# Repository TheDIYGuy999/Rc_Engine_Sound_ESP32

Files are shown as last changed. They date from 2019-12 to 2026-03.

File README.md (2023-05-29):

# This is an Arduino RC engine sound & light controller for ESP32





It's based on the ATmega 328 version: https://github.com/TheDIYGuy999/Rc_Engine_Sound
and on bitlunis Halloween example: https://github.com/bitluni/MotionPumpkin

Wiring and software installation instructions see further down.
Arduino IDE or Visual Studio Code (with Platform IO extension) are supported.

Video series: https://www.youtube.com/playlist?list=PLGO5EJJClJBCjIvu8frS7LrEU3H2Yz_so

************************************************************************
You can find the changes in the [Changelog](documentation/Changelog.md).
************************************************************************

Discussion and support thread (in German & English): https://www.rc-modellbau-portal.de/index.php?threads/esp32-arduino-rc-sound-und-licht-controller.7183/

Fully assembled, tested and working 30 pin SMD version with switch mode PSU & display connector.
Order it here: https://www.pcbway.com/project/shareproject/Arduino_RC_engine_sound_light_controller_for_ESP32_a9334731.html


New: STL data for nice 3D printed housing available:
https://thediyguy999.github.io/TheDIYGuy999_ESP32_Web_Flasher/products.html
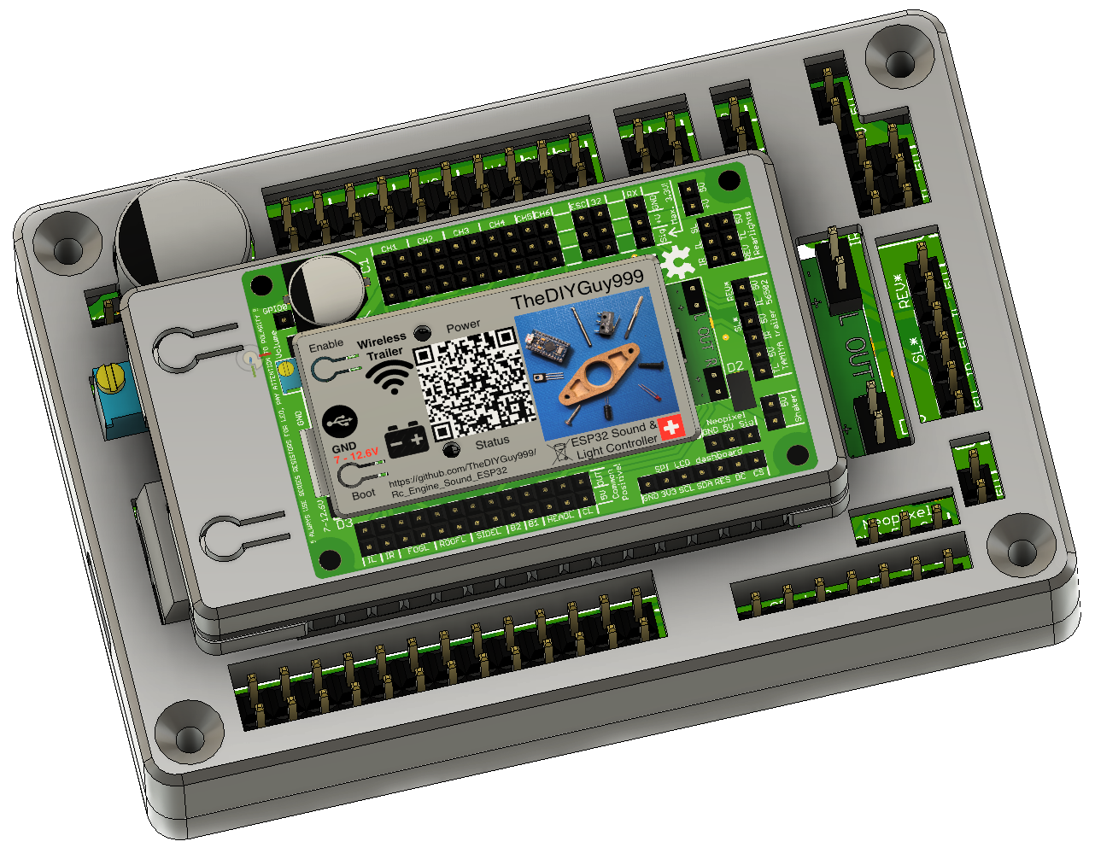
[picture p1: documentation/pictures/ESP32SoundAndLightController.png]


New: Compact version for trailer or tractor:
https://thediyguy999.github.io/TheDIYGuy999_ESP32_Web_Flasher/products.html
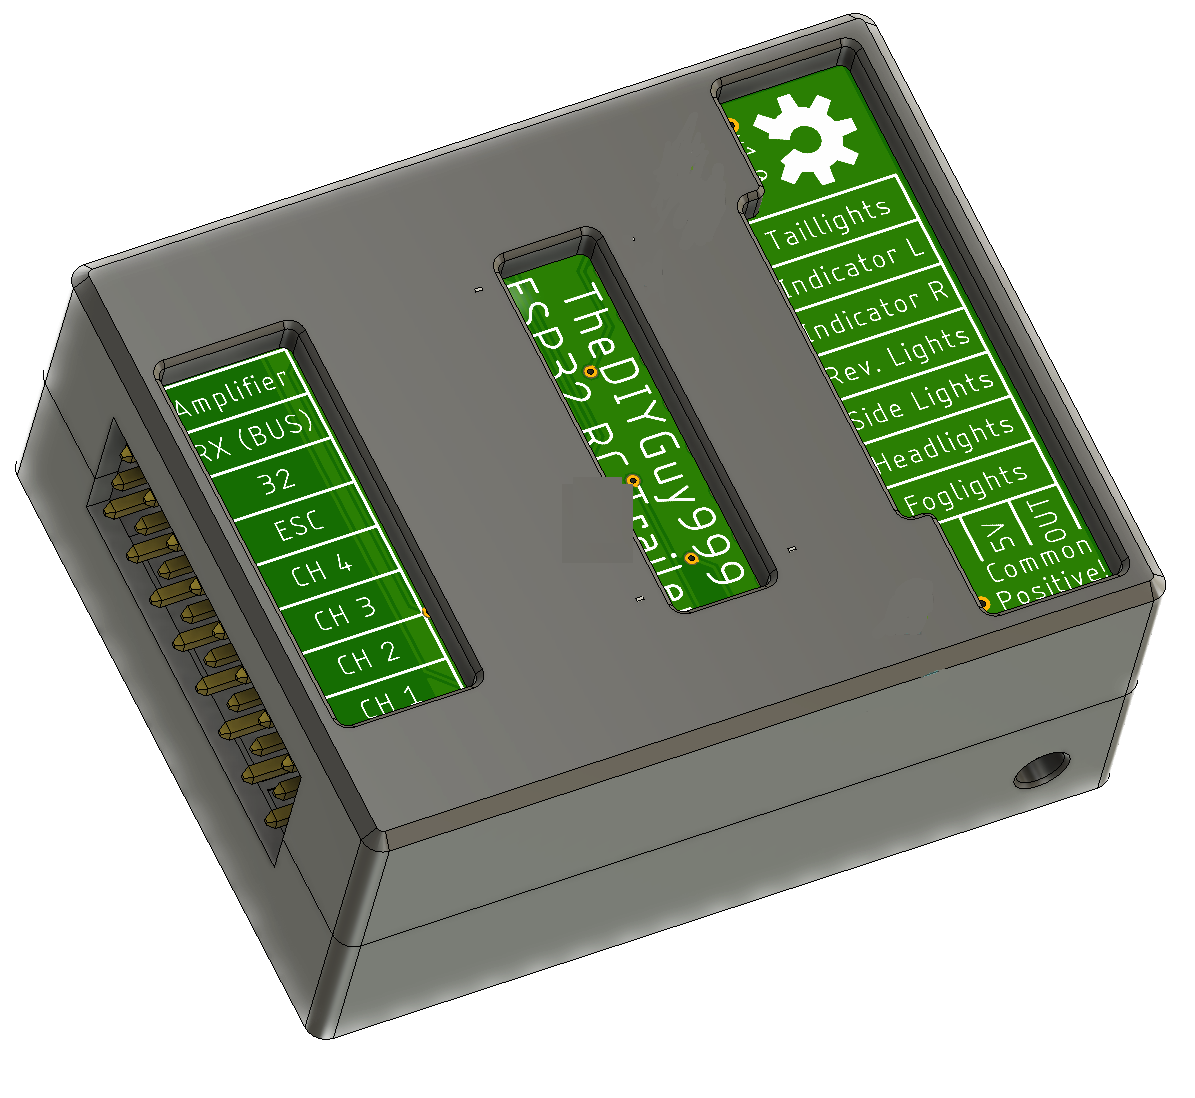
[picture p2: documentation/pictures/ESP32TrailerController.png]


New: RZ7886 7A ESC:
https://thediyguy999.github.io/TheDIYGuy999_ESP32_Web_Flasher/products.html
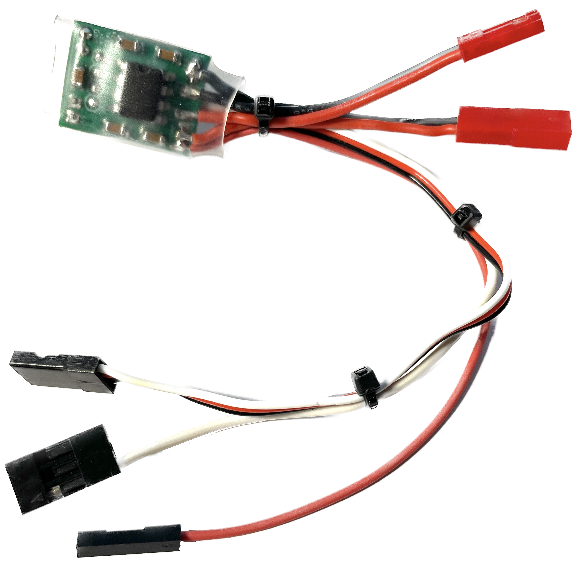
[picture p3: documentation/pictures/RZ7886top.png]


New: wireless built-in configuration website 192.168.4.1
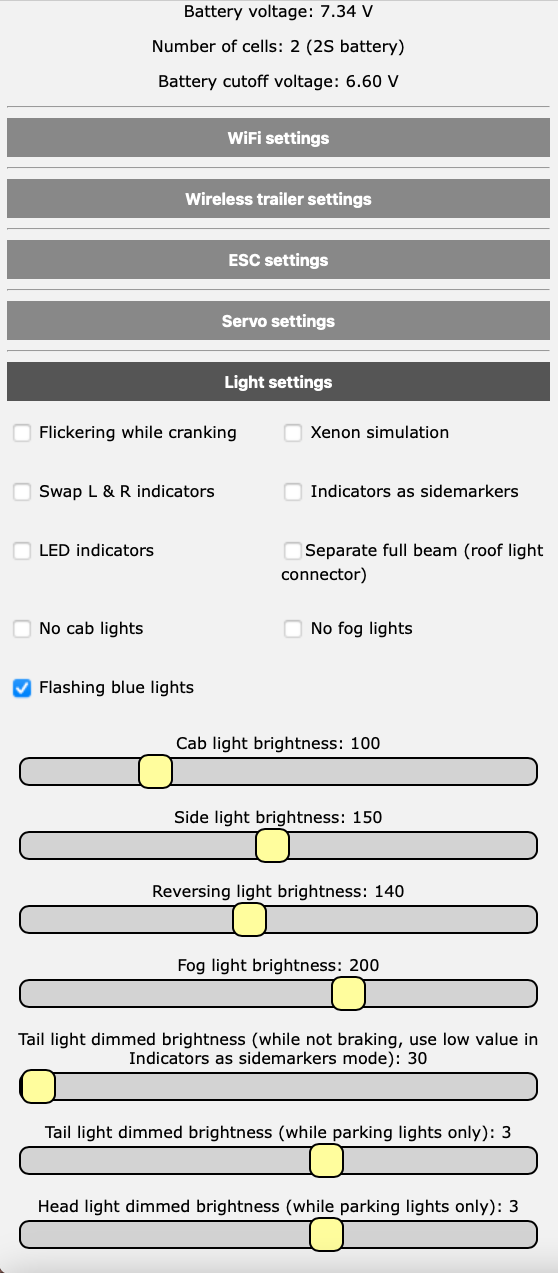
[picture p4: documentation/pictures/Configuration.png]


New: LCD dashboard (original by Frevic)
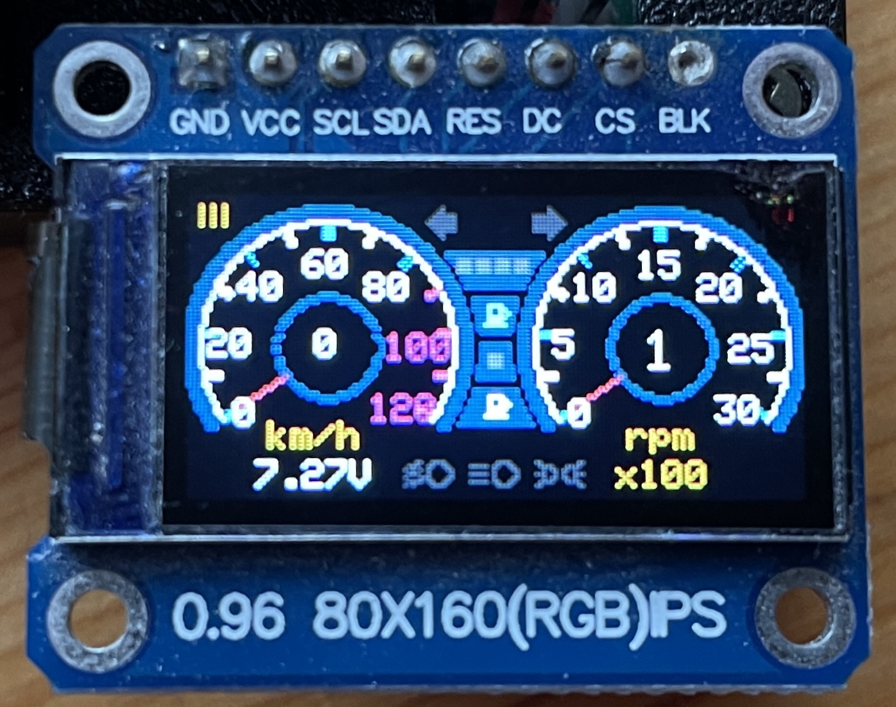
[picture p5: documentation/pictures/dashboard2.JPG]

https://www.facebook.com/profile.php?id=100066616574355

LCD dashboard (original by Gamadril)
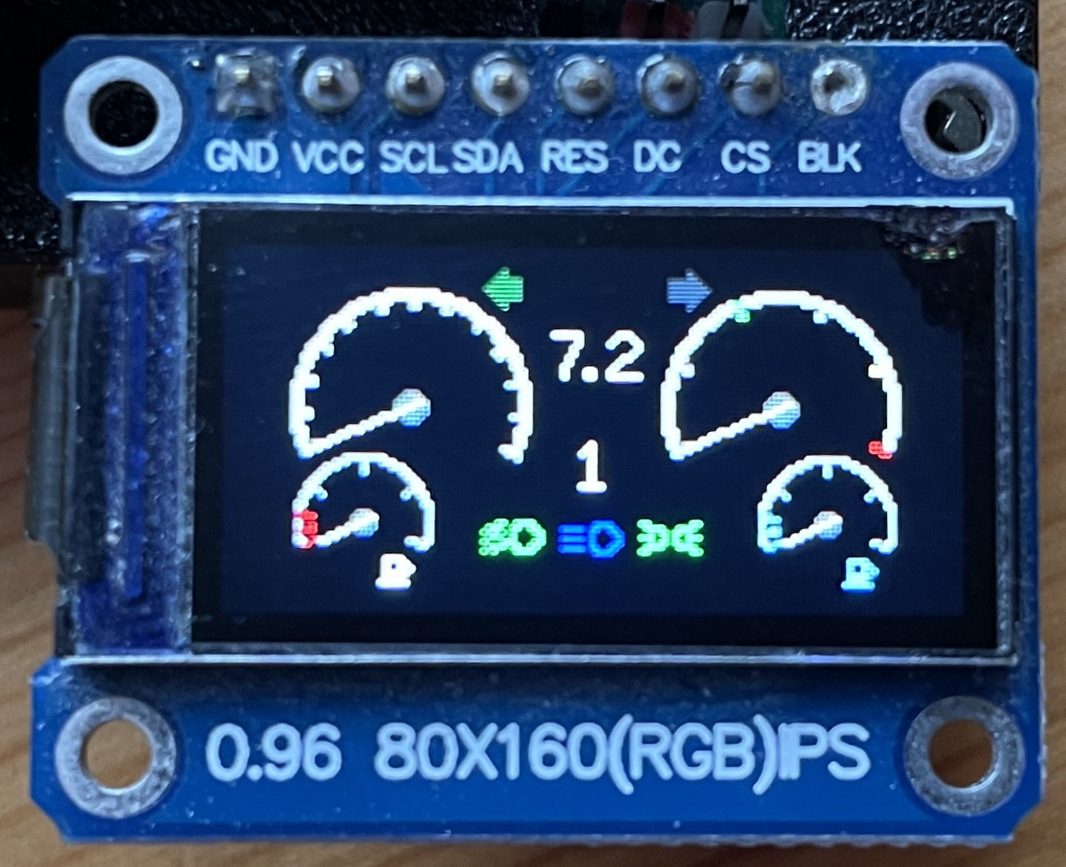
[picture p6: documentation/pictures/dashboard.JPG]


Fully assembled, tested and working 30 pin SMD version, manufactured and pre-assembled by https://www.pcbway.com
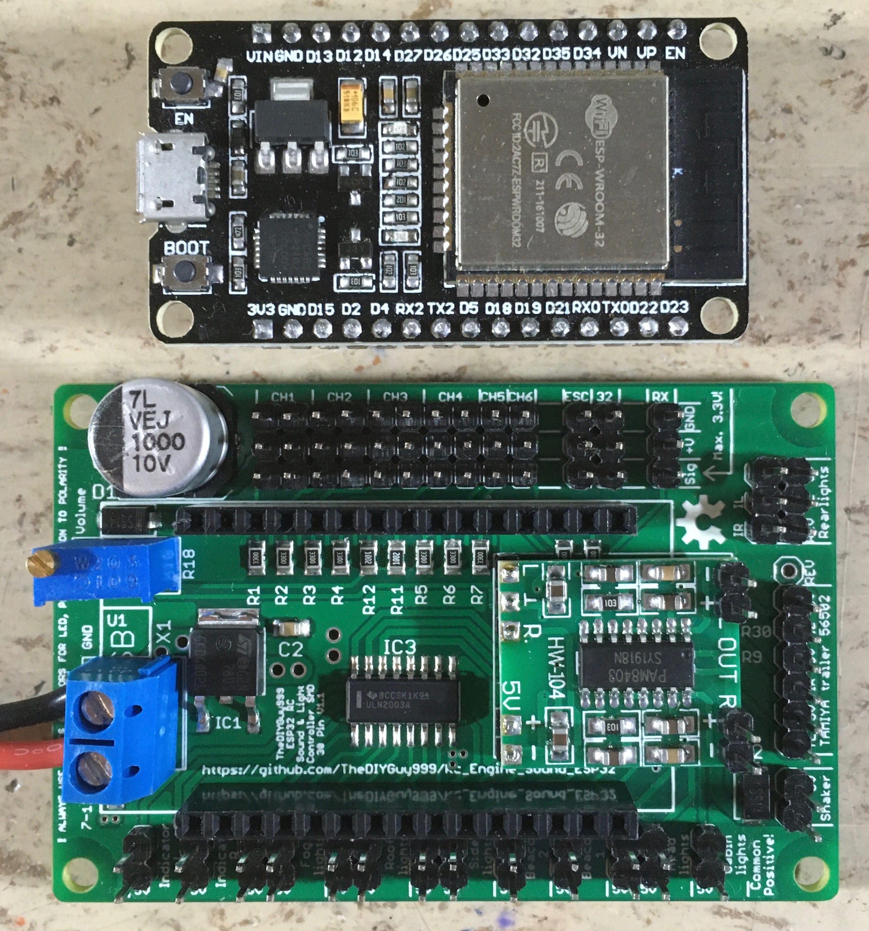
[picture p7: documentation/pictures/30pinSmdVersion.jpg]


Fully assembled, tested and working 30 pin thru hole version
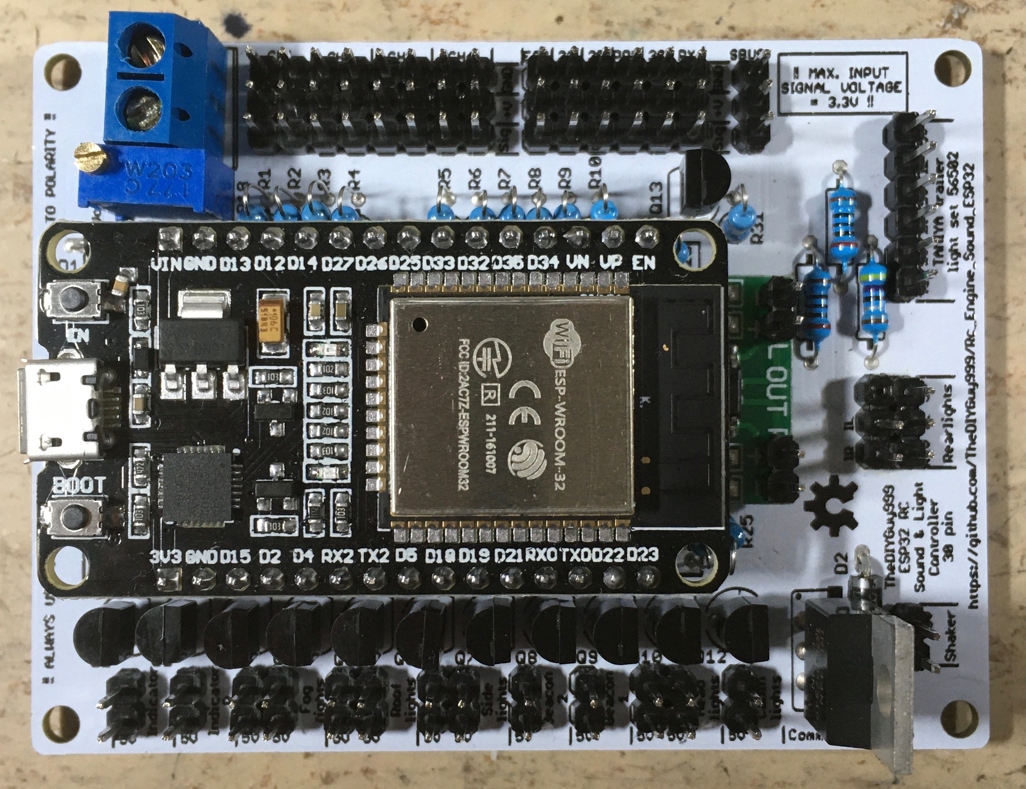
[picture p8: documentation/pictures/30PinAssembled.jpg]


Compact version for excavator (IBUS & sound only, supplied by 6V BEC)
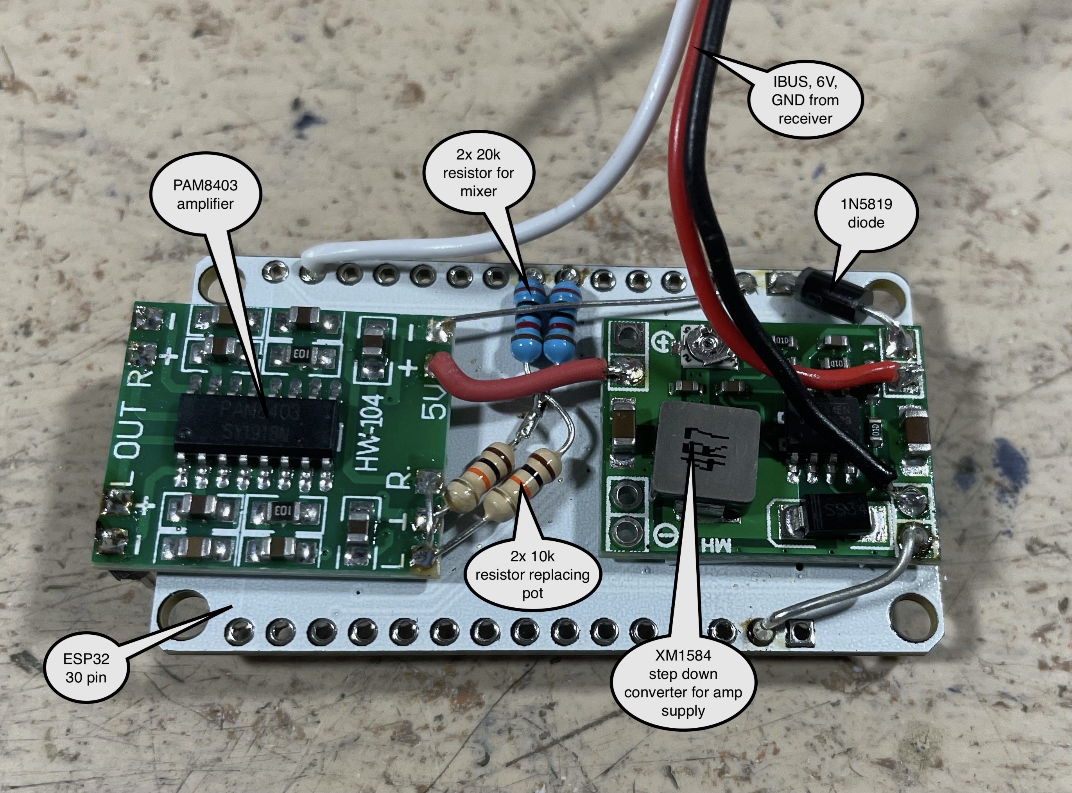
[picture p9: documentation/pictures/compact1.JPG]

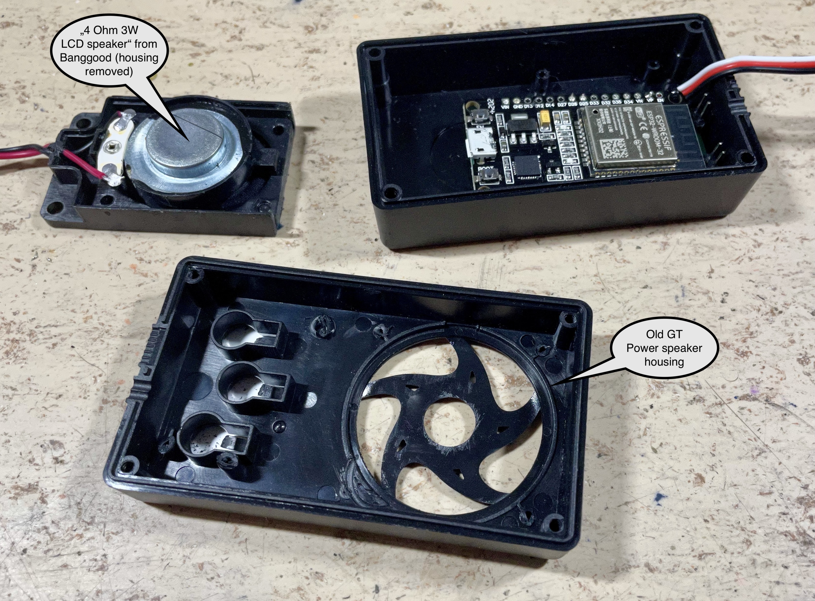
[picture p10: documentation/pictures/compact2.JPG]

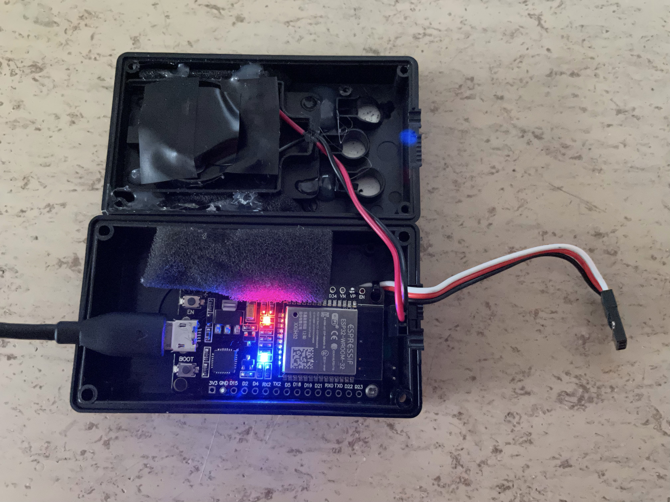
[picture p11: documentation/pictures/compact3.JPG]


## Features:
- Unique vehicle mass inertia simulation (connect your crawler type ESC to pin 33). Throttle output is altered during shifting of a mechanical 3 speed transmission for smooth shifting, gear protection and realistic sound. Works just fine with TAMIYA 3 speed transmissions. Should work as well with crawler 2 speed transmissions. The ESC is controlled by a state machine with the following states: driving forward & reverse (varible acceleration, depending on throttle position), neutral, braking forward & reverse (variable deceleration with fine granularity, according to "reverse throttle" position). It also allows to control the brake lights, the brake sound, the reversing light & the reversing beep sound properly. Acceleration & deceleration (coasting & braking) are adjustable separately for each gear to ensure maximum realism.
- Unique "virtual clutch" allows to rev the engine below an adjustable ESC output speed. Above, the clutch engages and ensures, that the engine sound is in synch with the wheel RPM. Sounds and behaves just great in combination with a shifting transmission!
- Simulated automatic transmission with torque converter (if your vehicle does not have a real shifting transmission)
- Simulated double clutch transmission
- simulated, manually shifted 3 speed transmission (new in v5.5)
- Virtual, switchable neutral allows to rev the engine while standing still
- Jake brake (simulated pneumatic engine brake, mainly used in US trucks)
- Tracked mode (dual throttle input on CH2 & CH3, for tanks, diggers etc. No ESC control support in this mode. (New in v4.5)
- Tank cannon sound & flash (New in v4.6)
- Triggering multiple latching and non latching actions (sounds, lights) per analog channel, using the rcTrigger library (New in v4.7, still experimental)
- Many selectable sounds: engine cranking, engine idling, engine revving, turbo whining, diesel ignition "knock", wastegate valve, horns, sirens, reversing beep, air brake, parking brake, gear shifting etc.
- Realistic engine sound is mixed together on the fly from up to 4 sounds: engine idling, turbo, wastegate (all with variable sampling rate), Diesel ignition knock (fixed sampling rate, so it does not vary in pitch)
- Load (throttle position) dependent volume sounds: idle, rev, Diesel knock
- Engine RPM dependent volume sounds: turbo, wastegate
- Dozens of engine & other sounds included, you can also compose your own, using Audacity and bitlunis conversion tool (link above)
- Engine RPM range and inertia adjustable, volume of all sounds adjustable, engine sounds separatly for load and idling.
- Many other paramerets can be adjusted. All adjustments are easily accessible in "adjustmentsXyz.h"
- Sound files up to 22'050Hz, 8bit, mono can be used
- Compatible input signals: PWM, PPM, SBUS (inverted & non inverted signals), IBUS
- Works best with a PAM8403 amplifier module, connected to pin 25 & 26, via 10kOhm resistors & a 10kOhm potentiometer (see schematic below)
- The engine RPM is calculated according to RC signal input on pin 13 *** CAUTION, 3.3V max. on all pins! *** 330 Ohm resistors on all I/O pins recommended!
- Non linear throttle curves can be generated in "curves.h"
- Light effects: headlights (high & low beam), tail lights, brake lights, fog lights, roof lights, cab lights, reversing light, indicators (turn signals), hazard lights, blue light etc. (max. 12 outputs)
- Engine vibration simulation, using a shaker motor with excentric weight: Strong vibration while cranking, medium wlile idling, slight while revving
- Adjustable volume (via remote)
- Use an ESP32, CPU frequency must be set to 240MHz
- Eagle schematic & board file included. Pre made Gerber files allow you to order your board easily.
- included, easy to use .wav to .h sound file converter
- Channels can easily be assigned, using "remoteSetup.h"
- Pre made configuration profiles for Flysky FS-i6X and Arduino Mirco RC remote (new in v.5.5)
- Variable length for horn & siren, using loop area in sound files (new in v5.6)
- BUS decoder for steering servo and shifting servo (connect servos to CH1 & CH2) pins
- Trailer coupler (5th wheel) servo can be connected to the CH4 pins (not in PWM communication mode)
- TAMIYA trailer presence switch can be connected to pin 32 (depending on "#define THIRD_BRAKELIGHT" setting in "6_adjustmentsLights.h" tab)
- Support for non linear throttle and steering curves (for more accurate control around center position). Use "EXPONENTIAL_THROTTLE" & "EXPONENTIAL_STEERING" in "2_adjustmentsRemote.h"
- Support for HOBBYWING Quicrun Fusion Motor / ESC combo. Use "#define QUICRUN_FUSION" in "3_adjustmentsESC.h"
- Support for winch, connected to CH3 (BUS communication mode only). Use "#define MODE2_WINCH" in "7_adjustmentsServo.h" The mode 2 button is then used to switch between horn / siren sontrol and winch control via CH4. The winch is controlled by an old RC servo driver board. The speed and neutral settings are done using "CH3L", CH3C" and CH3R" positions.
- Support for LCD dashboard
- Support for 2812 Neopixel LED (GPIO0)
- Support for hydlaulic excavators (hydraulic pump, hydraulic flow, track rattling sounds). Use #define FLYSKY_FS_I6S_EXCAVATOR profile for remote
- ESP-NOW based 2.4 GHz wireless trailer control support
- An RZ7886 motor driver IC can be used instead of a standard crawler type RC ESC
- Battery low discharge protection options
- Switchable crawler mode (with just minimal virtual inertia)
- Wireless configuration website 192.168.4.1

## On the todo list:
- cornering lights (on the beacon outputs)
- Hazards switching on, if engine off in AUTO_LIGHTS mode

## Known issues:
- Arduino IDE 1.8.7 or older is not supported and will cause compiler errors!
- The ESP32 does not work on macOS Big Sur 11.x, but this issue can be fixed easily as described here: [Big Sur Fix](BigSurFix.md) (for v1.04)
- macOS Monterey 10.3 does not include Python 2 anymore. For Arduino IDE, you have to install Python 3 and to change the path in pPlatform.txt according to:
https://forum.arduino.cc/t/mac-os-update-killed-esp32-sketch/969580/24

## How to create new .h sound files:

### Audacity:
- import the WAV sound file you want in Audacity
- convert it to mono, if needed
- on the bottom left, select project frequency 22'050Hz
- search for a cyclic pattern in the idle sound (the amount of ignition pulses is usually the same as the cylinder number), cut the "idle" sample to exactly this length, have a close look at the zero crossings to avoid clicking noises. The loudest peak should always be at the end of the sample.
- do the same with the "rev" sound. It will be 2 - 4 times shorter than the "idle" sample, depending on the engine and rpm of the "rev" sample
- change the "Rate" (dropdown on the left of the sample) of the "rev" sample, until the length is the same as in the "idle" sample. This is very important!
- duplicate a part of the "rev" sample (the one with the original, unchanged "Rate" speed). This is the "knock" sample. Cut it to this max length: "Idle" length / number of cylinders / rpm range "MAX_RPM_PERCENTAGE" (usually 2 - 4 or 200 - 400%)
- adjust the volume of all samples, so that the entire dynamic range is used
- you may also want to apply high pass or low pass filters to fine tune the sound
- select > export audio > selected audio > WAV > 8-bit-PCM

### Convert the .wav file with the modified converting tool (new in v5.2):
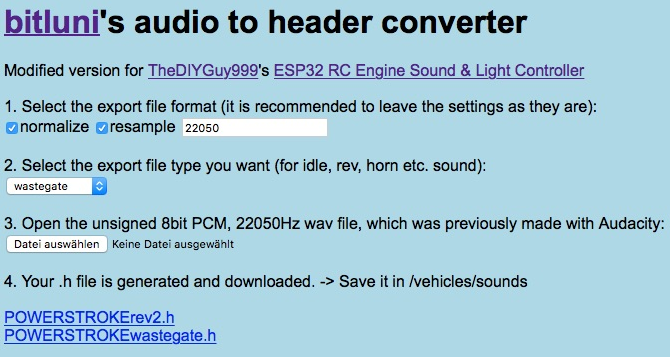
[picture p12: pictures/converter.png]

- open the included "Audio2Header.html" converter in your browser. It is located in the "tools" folder
- adjust the export file format (no changes required)
- select the export file type, depending on the sound you are converting (idle, rev, horn etc.)
- open the wav file you want to convert
- a .h file is generated and downloaded
- move it to your "sketch/vehicles/sounds" directory

### Include the new header file with your sound in your vehicle preset, adjust settings until you are happy:
- include this .h file in "Adjustments.h" > "yourVehiclePreset.h"
- knock sound settings:
  - "dieselKnockInterval" = number of cylinders
  - uncomment "V8" for V8 engines, R6 for inline 6 engines or "V2" for V2 (Harley) engines
  - adjust "dieselKnockAdaptiveVolumePercentage" (how loud the "silent" knock pulses are compared with the loud ones), only active, if defined "V8", "R6"  or "V2"
- play with the other volumes, start-, end- and switch-points until you are happy
- the "rev" sound is optional and only active, if "REV_SOUND" is defined (// removed)
- adjust the transition from the "idle" to the "rev" sound, using "revSwitchPoint", "idleEndPoint", "idleVolumeProportionPercentage". This step is very important and can make a huge difference!

### Compile the new sketch:
- compile and upload the sketch in Arduino IDE
- the new sound should now be ready

## Schematic example (use PDF for current version!):
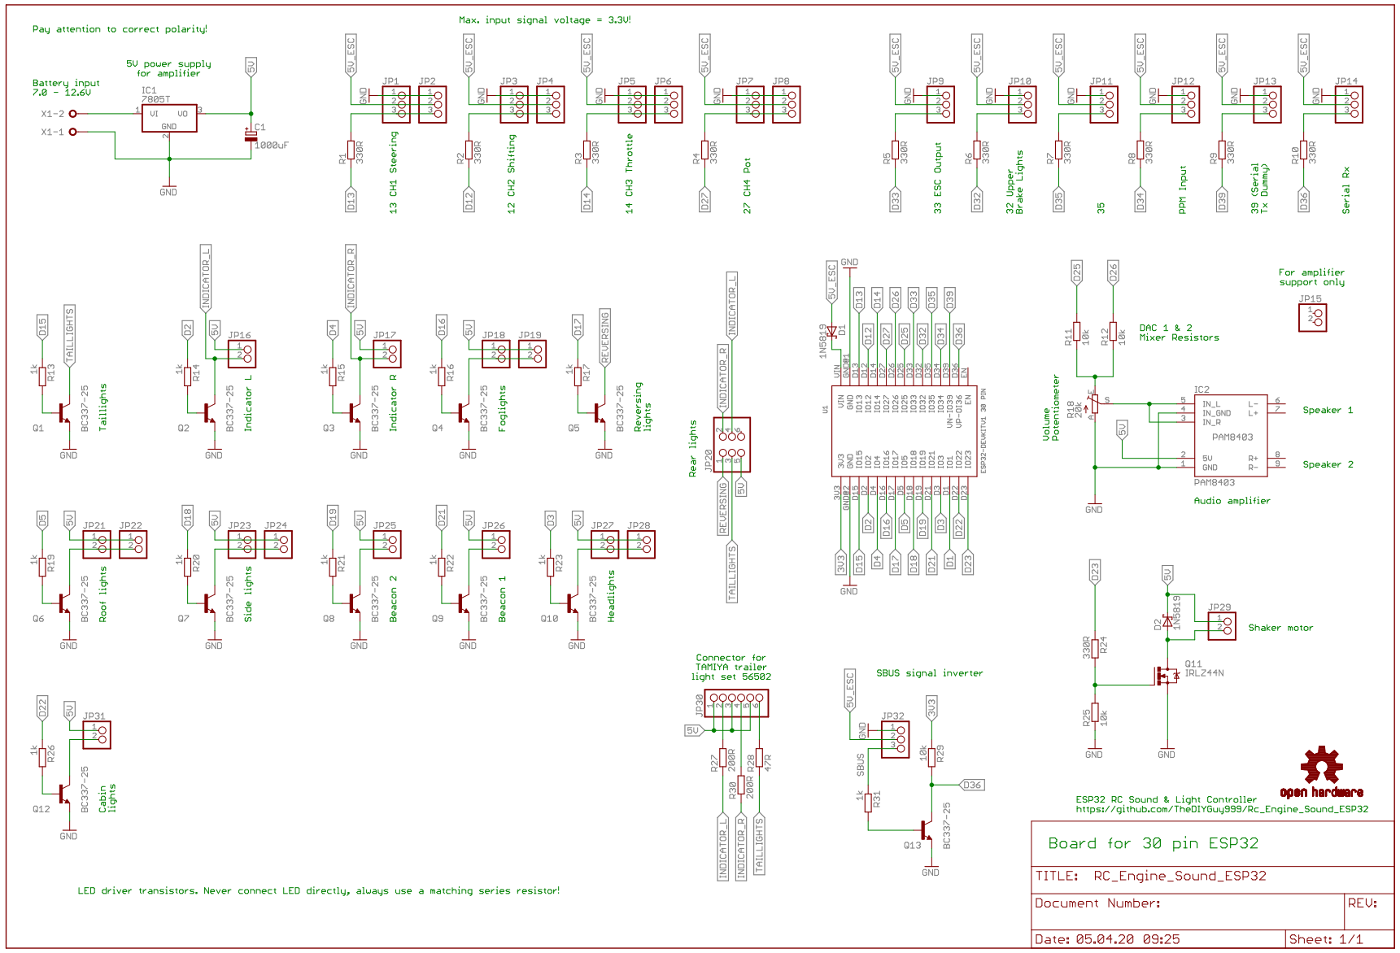
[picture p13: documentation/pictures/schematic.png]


## PCB
### Included PCB files:
- See hardware folder

### Recommended manufacturer:
https://www.pcbway.com (including SMD assembling service, use Gerbers.zip for board, it also includes BOM. xlsx and CPL.xlsx, if you want to use the SMT assembling service)
How to order pre assembled boards see /Eagle_PCB/How To Order Your PCB.pdf

### The easiest way to order the 30pin SMD version with display connector:
https://www.pcbway.com/project/shareproject/Arduino_RC_engine_sound_light_controller_for_ESP32_a9334731.html

### Assembling tutorial (for the 30 pin SMD version without display connector):
https://www.youtube.com/watch?v=csQgTfxRd8Y&t=2s

### Assembling tutorial (for the 36 pin version):
https://www.youtube.com/watch?v=Vfaz3CzecG4&list=PLGO5EJJClJBCjIvu8frS7LrEU3H2Yz_so&index=13

## Wiring:
### Before you begin:
- This device is not protected against wrong polarity!
- Always use series resistors for LED headers (except TAMIYA trailer header)
- Maximum input voltage on "Sig" pins = 3.3V (be careful with very old receivers, which may deliver 5V)
- It is recommended to use a fuse between your battery and the sound controller / ESC

### Supply for audio amplifier, shaker motor and LED:
- Use an Y-cable between your battery, your ESC and The "X1" terminal. Battery voltage range is 7 - 12.6V

### Supply for ESP32:
- The ESP32 is not supplied through the "X1" terminal
- It can be supplied through the Micro USB header
- or through the +V and GND pin row on the top of the board (the voltage is usually coming from the BEC in your ESC, which needs to be connected to the "ESC" header)

### ESC wiring:
- Connect a Hobbywing 1080 ESC to the ESC header (GND, V+ and Sig)
- Adjust the ESC parameters, using the programming card as described on the top of "Adjustments.h"
- I do not recommend any other ESC
- The ESC is controlled by the cound controller, rather than directly by the receiver. This allows to use the unique "virtual inertia" feature. NOTE: Use this feature at your own risk! I'm not responsible, if any damage is caused. It's running very stable and I never had an issue, but you never know.
- "escPulseSpan" can be used to limit the top speed of your vehicle. 500 = not limited, anything above 500 will limit the top speed

### Receiver wiring for PWM servo signals (the most common wiring):
- Channel assignment according to "remoteSetup.h" and remoteSetup.xlsx", easily adjustable (new in v5.5). It is important to plug in the wires according to the channel assignment
- CH5 & 6 are coming in via the "35" & PPM" headers
- At least one CH needs to be connected, using a 3 pin wire, so that GND and V+ are connected as well (receiver supply)
- CH1 - 4 headers are pairs, wired in parallel. This allows to feed servo signals through, eliminating the need for Y-cables
- Note that you need to change the configuration as described below, if you want to use this wiring method

### Receiver wiring for PPM signals:
- Internal channel assignment as above
- Connect a 3 pin wire fom your receiver PPM header to the RX (changed in v5.5, was PPM) header on the sound controller (Sig, V+, GND)
- Note that you need to change the configuration as described below, if you want to use this wiring method
- 8 channels can be read in this mode

### Receiver wiring for SBUS signals (recommended):
- Internal channel assignment as above
- Connect a 3 pin wire fom your receiver SBUS header to the SBUS header on the sound controller (Sig, V+, GND)
- The "Sig" pin on the SBUS header is 5V tolerant
- 13 channels can be read in this mode

### Receiver wiring for IBUS signals:
- Internal channel assignment as above
- Connect a 3 pin wire fom your receiver IBUS header to the RX header on the sound controller (Sig, V+, GND)
- 13 channels can be read in this mode

### Speakers
- 4 or 8 ohms speakers are compatible
- You can use one or two speakers
- never use two speakers in parallel on a single header
- never use two headers in parallel to drive one speaker
- never connect capacitors to the speaker headers

### LED
- The LED need to be wired "common positive". This means, the long LED legs are all connected together and connect to the 5V rail, coming from the on board regulator
- All LED (except the ones, which are connected to the TAMIYA trailer connector) need a series resistor
- Calculate the reqired resistor according to: http://ledcalc.com (supply voltage = 5V)
- It is not recommended to wire LED in parallel, sharing the series resistor
- Support for WS2812 Neopixel LED (details and wiring see "6_adjustmentsLights.h")

### LCD dashboard
- See "9_adjustmentsDashboard.h"

### Shaker
- The shaker is used for engine vibration simulation. The speed can be adjusted in the vehicle configuration and will vary depending on the engine state and rpm
- It needs to be connected to the "shaker" header and is supplied by the on board 5V regulator. The negative side is switched by the on board mosfet
- Please note, that the used mosfet needs to be a logic level type. Otherwise the shaker will not work!
- The motor should not draw more than about 300mA @ 5V. I'm using a shaker motor from GT Power.

### RZ7886 7A DC motor driver instead of an ESC:
It is intended for smaller scale vehicles like WPL

#### Prototype:
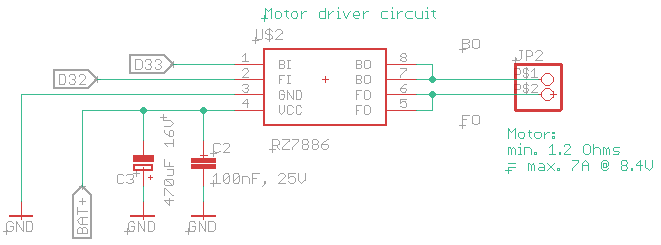
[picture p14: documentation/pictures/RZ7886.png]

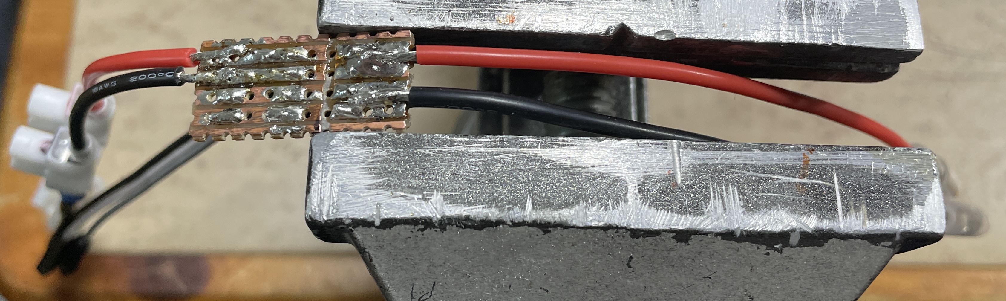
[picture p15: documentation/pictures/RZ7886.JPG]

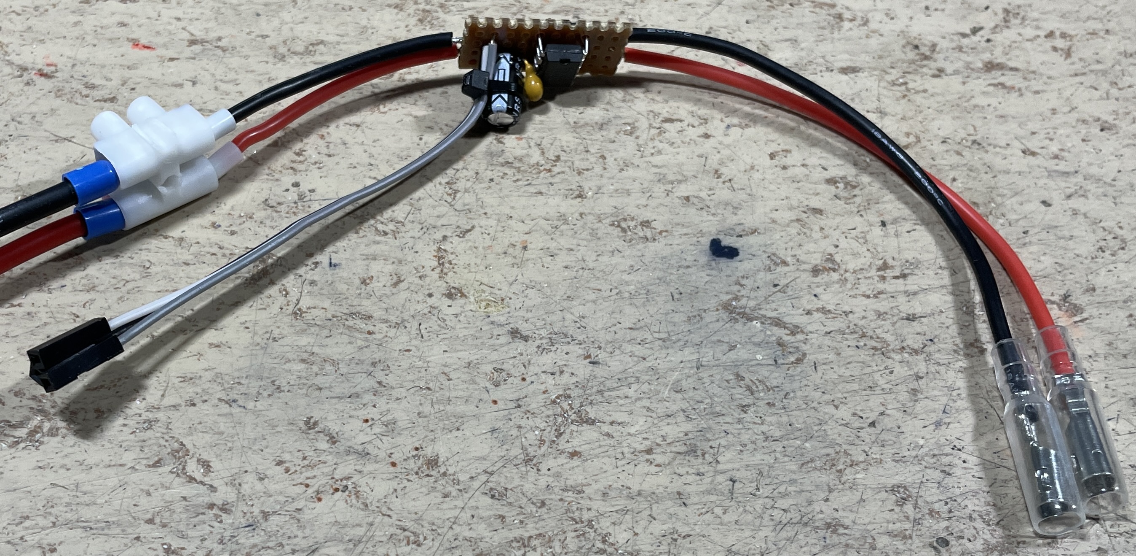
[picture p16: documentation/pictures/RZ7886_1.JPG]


#### Order your motor driver PCB here:
https://www.pcbway.com/project/shareproject/RZ7886_based_ESC_for_ESP32_Sound_and_Light_Controller_f8f4a805.html

## Software:
### Required software for code uploading and editing:
- Arduino IDE (not recommnded): https://www.arduino.cc/en/Main/Software
- or Visual Studio Code with PlatformIO extension (recommended): https://code.visualstudio.com
- Visual Studio also requires this software (restart VS Code afterwards) in order to be able to synchronise libraries: https://git-scm.com/download

### Downloading and preparing the code with Arduino IDE:
- Download the code from here (hit "Code > Download zip"): https://github.com/TheDIYGuy999/Rc_Engine_Sound_ESP32
- Unzip the folder, if required
- Remove the "-master" part of the folder name
- Install libraries and board definitions below first, restart Arduino IDE
- Open "scr.ino" with a double click (Arduino IDE should start)

### Required ESP32 board definition (not required, if Visual Studio Code is used as IDE):
- Install it according to: https://randomnerdtutorials.com/installing-the-esp32-board-in-arduino-ide-windows-instructions/
- Use v1.04, v1.05 or newer are causing reboot issues!
- Adjust settings according to:
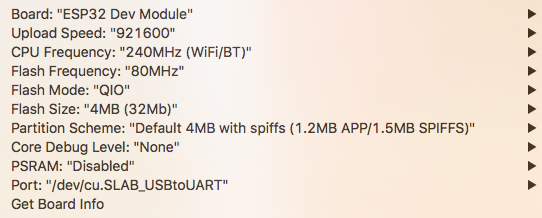
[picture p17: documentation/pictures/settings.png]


### Required libraries. You need to install ALL of them, if using Arduino IDE. Not required, if Visual Studio Code is used as IDE:
- statusLED: https://github.com/TheDIYGuy999/statusLED
- SBUS: https://github.com/TheDIYGuy999/SBUS
- rcTrigger: https://github.com/TheDIYGuy999/rcTrigger
- IBUS: https://github.com/bmellink/IBusBM
- TFT: https://github.com/Bodmer/TFT_eSPI
- FastLED: https://github.com/FastLED/FastLED    

Download them in the same manner as the main code above. Store the folders in your "Arduino/libraries" path.
Install them according to: https://www.arduino.cc/en/Guide/Libraries

### Uploading the code to the board:
- IMPORTANT: Depending on your board, you may have to press and hold the "BOOT" button, if the IDE just shows "Connecting........_____...." Release it, as soon as the upload starts.
- On macOS Big Sur, you need to apply the following fix (Arduino IDE only):  [Big Sur Fix](BigSurFix.md)

### Visual Studio Code (instead of Arduino IDE) overiew:
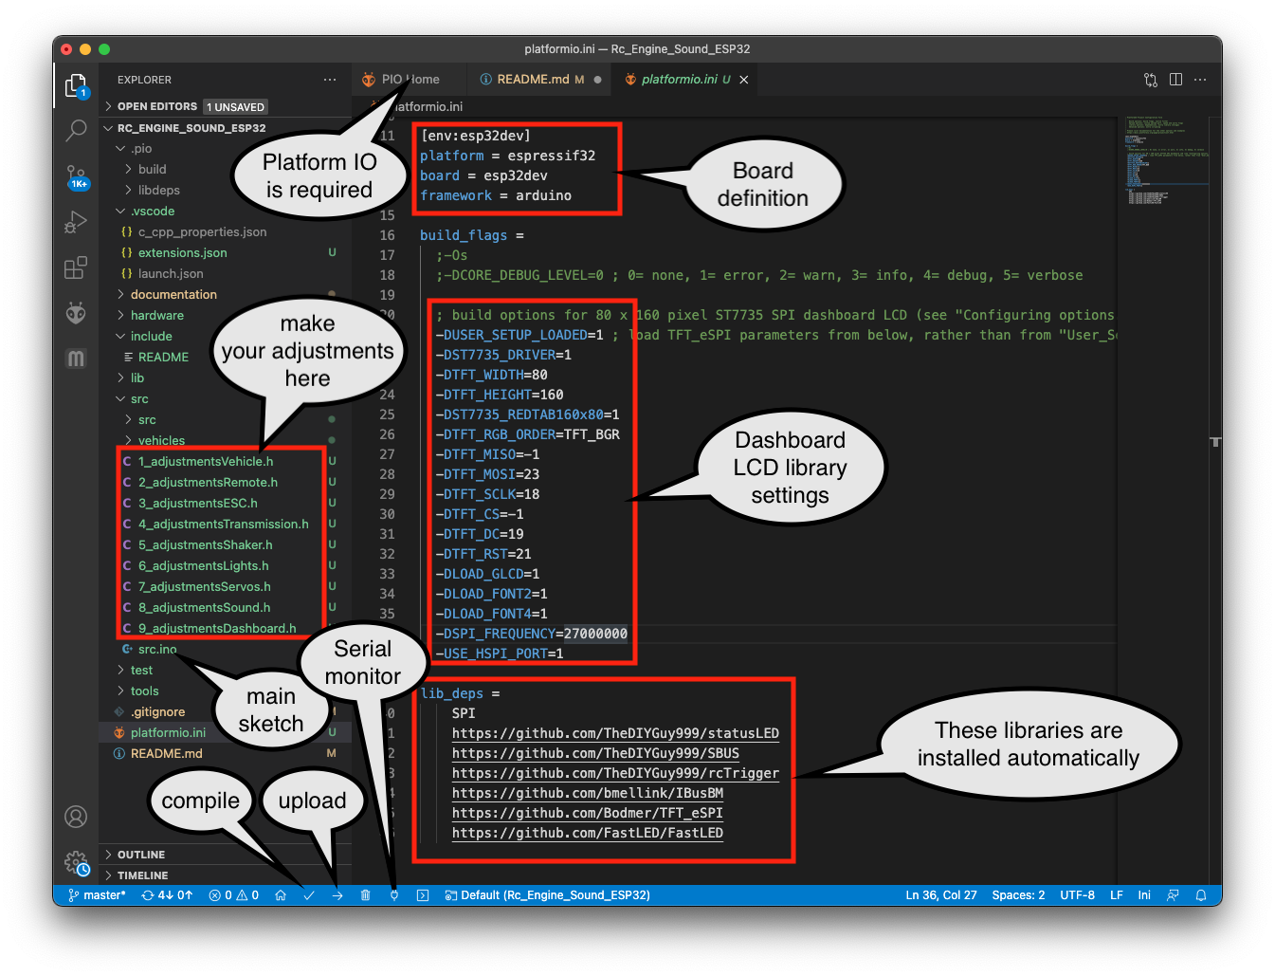
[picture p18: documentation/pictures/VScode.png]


## Adjusting things in "X_Xyz.h":
### Vehicle selection:

Note, that in v5.5 the former "Adjustments.h" configuration file was divided into multiple files.

Uncomment (remove //) the vehicle you want in "Adjustments.h". Never uncomment more than one vehicle!
Note, that you need to re-upload the code after you changed the settings. Otherwise it will not take effect.
Select >Sketch > Upload to upload the code. Important! Always lift your vehicle off the ground while uploading.

If you want to make a new vehicle, copy vehicles/00_Master.h, store it with your vehicle name. Then edit the settings as you like, add links to the sound files you want.
Afterwards add a link to your vehicle.h (see examples below) and uncomment it

```
#include <Arduino.h>

// VEHICLE SETTINGS ****************************************************************************************************
// Select the vehicle preset you want (uncomment the one you want, remove //, never more than one)

// Master --------
//#include "vehicles/00_Master.h" // This master preset file contains all available sound files, which are not used in existing vehicle presets

// US trucks --------
//#include "vehicles/CaboverCAT3408.h" // Cabover truck with Caterpillar 3408 V8 Diesel
//#include "vehicles/PeterbiltDetroit8v92.h" // Peterbilt 359 with Detroit 8V92 V8 2 stroke Diesel
//#include "vehicles/KenworthW900ADetroit8V71.h" // Kenworth W900A with Detroit 8V71 V8 2 stroke Diesel
//#include "vehicles/KenworthW900ACAT3408.h" // Kenworth W900A with Caterpillar 3408 V8 Diesel (King Hauler)
//#include "vehicles/CAT3408OpenPipes.h" // Kenworth W900A with Caterpillar 3408 V8 Diesel and open pipes
//#include "vehicles/KenworthW900ACAT3408new.h" // Kenworth W900A with Caterpillar 3408 V8 Diesel (good bass speaker required)
//#include "vehicles/KenworthCummins335.h" // 1950ies Kenworth with Cummins 335 R6 Diesel
//#include "vehicles/MackSuperLiner.h" // MACK Super Liner
//#include "vehicles/M35.h"// AM General M35 "deuce and a half" military truck, turbocharged R6 universal fuel engine
//#include "vehicles/US_Firetruck.h"// US firetruck with CAT3408 V8 and Allison 6 speed automatic (horn & siren loop capable)
//#include "vehicles/FreightlinerCummins350.h" // Freightliner Cabover with Cummins 350 R6 Diesel

// EU trucks --------
//#include "vehicles/Tatra813.h" // Tatra 813 8x8 V12 Diesel military truck (old version for comparison, don't use it)
//#include "vehicles/Tatra813new.h" // Tatra 813 8x8 V12 Diesel military truck
//#include "vehicles/UnimogU1000.h" // Umimog U 1000 with turbocharged R6 Diesel incl. Feuerwehr "Martinshorn" siren
//#include "vehicles/MercedesActros1836.h" // Mercedes Actros 1863 or 3363 truck with R6 Diesel
//#include "vehicles/MercedesActrosV6.h" // Mercedes Actros V6 Race Truck incl. tire squealing
//#include "vehicles/ScaniaV8_50ton.h" // SCANIA V8 50 ton truck. Unknown model. Bad quality!
//#include "vehicles/ScaniaV8.h" // SCANIA V8 truck, unknown model
//#include "vehicles/1000HpScaniaV8.h" // 1000 HP SCANIA V8 truck with open pipes. Insane sound! Good bass speakers reqired
//#include "vehicles/Scania143.h" // SCANIA 143 V8 - the legend! The best sounding in my opinion
//#include "vehicles/ScaniaV8Firetruck.h" // SCANIA V8 firetruck, automatic Allison 6 speed transmission with torque converter, "Martinshorn" siren
//#include "vehicles/VolvoFH16_750.h" // Volvo FH16 750 truck. Inline 6, 750 horses, open pipes!
//#include "vehicles/VolvoFH16_OpenPipe.h" // Volvo FH truck. Inline 6, open pipes, alternative version
//#include "vehicles/ManTgx.h" // MAN TGX 680 V8 truck
//#include "vehicles/ManKat.h" // MAN KAT V8 Diesel German Bundeswehr military truck
//#include "vehicles/MagirusDeutz256.h" // Magirus Deutz 256 air coolded V8 Diesel truck
//#include "vehicles/MagirusMercur125.h" // Magirus Mercur air coolded V6 Diesel truck
//#include "vehicles/Saurer2DM.h" // Swiss Saurer 2DM R6 Diesel truck

// Russian trucks --------
//#include "vehicles/Ural4320.h" // URAL 4320 6x6 V8 Diesel military truck
#include "vehicles/Ural375D.h" // URAL 375D 6x6 V8 petrol military truck
//#include "vehicles/URAL375.h" // URAL 375D 6x6 V8 petrol military truck (new version with better V8 sound, but good bass speaker required)
//#include "vehicles/GAZ66.h" // GAZ-66 V8 petrol military truck

// Russian tanks -------
//#include "vehicles/IS3.h" // IS-3 WW2 battle tank, V12 Diesel (dual ESC mode, good bass speaker required)

// Tractors -------
//#include "vehicles/KirovetsK700.h" // Russian Kirovets K700 monster tractor. Extreme turbo sound!

// Excavators -------
//#include "vehicles/Caterpillar323Excavator.h" // Caterpillar 323 excavator (use "FLYSKY_FS_I6S_EXCAVATOR" remote profile)

// Dumpers -------
//#include "vehicles/Benford3TonDumper.h" // Benford 3 ton dumper

// US motorcycles --------
//#include "vehicles/HarleyDavidsonFXSB.h" // Harley Davidson FXSB V2 motorcycle

// US cars --------
//#include "vehicles/ChevyNovaCoupeV8.h" // 1975 Chevy Nova Coupe V8
//#include "vehicles/1965FordMustangV8.h"// 1965 Ford Mustang V8
//#include "vehicles/Chevy468.h" // Chevy 468 big block V8

// EU cars --------
//#include "vehicles/VwBeetle.h" // VW Käfer / Beetle
//#include "vehicles/JaguarXJS.h" // Jaguar XJS V12, manual transmission
//#include "vehicles/JaguarXJSautomatic.h" // Jaguar XJS V12, automatic transmission
//#include "vehicles/MGBGtV8.h" // MGB GT V8, manual transmission
//#include "vehicles/LaFerrari.h" // Ferrari LaFerrari, V12, 6 speed double clutch transmission

// US SUV & Pickups --------
//#include "vehicles/JeepGrandCherokeeTrackhawk.h" // Jeep Grand Cherokee Trackhawk V8 monster SUV with supercharger, 6 speed automatic
//#include "vehicles/FordPowerstroke.h" // Ford Powerstroke 7.3l V8 Diesel, 6 speed automatic (good bass speaker required)
//#include "vehicles/RAM2500_Cummins12V.h" // Dodge RAM 2500 with inline 6, 12V Cummins 5.9l Diesel, manual transmission
//#include "vehicles/RAM2500_Cummins12Vautomatic.h" // Dodge RAM 2500 with inline 6, 12V Cummins 5.9l Diesel, automatic transmission
//#include "vehicles/GMCsierra.h" // GMC Sierra V8 pickup, 3 speed automatic transmission
//#include "vehicles/ChevyNovaCoupeV8_P407.h" // 1975 Chevy Nova Coupe V8, special version for HG-P407, 3 speed automatic transmission
//#include "vehicles/JeepWranglerRubicon392V8.h" // 2021 Jeep Wrangler Rubicon HEMI 392 V8 (starter needs rework)
//#include "vehicles/JeepWranglerRubicon392V8_2.h" // 2021 Jeep Wrangler Rubicon HEMI 392 V8 (insane bass!)

// EU SUV --------
//#include "vehicles/DefenderV8Automatic.h" // Land Rover Defender 90 V8 automatic (very nice V8 with lots of bass)
//#include "vehicles/DefenderV8OpenPipeAutomatic.h" // Land Rover Defender 90 V8 automatic, open pipes (optimised for smaller speakers)
//#include "vehicles/DefenderV8CrawlerAutomatic.h" // Land Rover Defender 90 V8 automatic crawler
//#include "vehicles/DefenderTd5.h" // Land Rover Defender 90 Td5 R5 Diesel

// Asian SUV --------
//#include "vehicles/LandcruiserFJ40.h" // Landcruiser Fj40 with inline 6 petrol engine
//#include "vehicles/LandcruiserFJ40Diesel.h" // Landcruiser Fj40 with inline 6 12H Turbo Diesel engine
//#include "vehicles/LandcruiserFJ40Diesel2.h" // Landcruiser Fj40 with inline 6 12H Turbo Diesel engine
//#include "vehicles/HiluxDiesel.h" // Hilux Diesel with inline 6 12H Turbo Diesel engine (for HG-P407)

// US locomotives --------
//#include "vehicles/UnionPacific2002.h" // Union Pacific 2002 SD70M locomotive with enormous, low revving 16 cylinder Diesel

// Planes --------
//#include "vehicles/MesserschmittBf109.h" // Messerschmitt BF 109 WW2 German V12 plane

// Generic Diesels --------
//#include "vehicles/generic6zylDiesel.h" // Generic inline 6 Diesel, no turbo, manual transmission (optimised for smaller speakers)
```

### Interface type (communication mode) selection:

Note, that the default communication mode is SBUS. You need to change it as follows, if you want to use classic RC servo signals.

#### PWM (classic RC signals on "CH1" - "CH4", "35" & "PPM" headers, the most common interface)
```
// COMMUNICATION SETTINGS **********************************************************************************************
// Choose the receiver communication mode (never uncomment more than one!) !!! ADJUST THEM BEFORE CONNECTING YOUR RECEIVER AND ESC !!!

// PWM servo signal communication (CH1 - CH4, 35, PPM headers, 6 channelschannelSetup.h) --------
// PWM mode active, if SBUS, IBUS and PPM are disabled (// in front of #define)

// SBUS communication (SBUS header, 13 channels. This my preferred communication protocol)--------
//#define SBUS_COMMUNICATION // control signals are coming in via the SBUS interface (comment it out for classic PWM RC signals)
boolean sbusInverted = true; // false = wired to non standard (inverted) SBUS signal (for example from "Micro RC" receiver)

// IBUS communication (RX header, 13 channels not recommended, NO FAILSAFE, if bad contact in iBUS wiring!) --------
//#define IBUS_COMMUNICATION // control signals are coming in via the IBUS interface (comment it out for classic PWM RC signals)

// SUMD communication (RX header, 12 channels, For Graupner remotes) --------
//#define SUMD_COMMUNICATION // control signals are coming in via the SUMD interface (comment it out for classic PWM RC signals)

// PPM communication (RX header, 8 channels, working fine, but channel signals are a bit jittery) --------
//#define PPM_COMMUNICATION // control signals are coming in via the PPM interface (comment it out for classic PWM RC signals)
```

#### PPM (multiple channels pulse pause modulation, wired to "RX" header, 8 channels)
```
// COMMUNICATION SETTINGS **********************************************************************************************
// Choose the receiver communication mode (never uncomment more than one!) !!! ADJUST THEM BEFORE CONNECTING YOUR RECEIVER AND ESC !!!

// PWM servo signal communication (CH1 - CH4, 35, PPM headers, 6 channelschannelSetup.h) --------
// PWM mode active, if SBUS, IBUS, and PPM are disabled (// in front of #define)

// SBUS communication (SBUS header, 13 channels. This my preferred communication protocol)--------
//#define SBUS_COMMUNICATION // control signals are coming in via the SBUS interface (comment it out for classic PWM RC signals)
boolean sbusInverted = true; // false = wired to non standard (inverted) SBUS signal (for example from "Micro RC" receiver)

// IBUS communication (RX header, 13 channels not recommended, NO FAILSAFE, if bad contact in iBUS wiring!) --------
//#define IBUS_COMMUNICATION // control signals are coming in via the IBUS interface (comment it out for classic PWM RC signals)

// SUMD communication (RX header, 12 channels, For Graupner remotes) --------
//#define SUMD_COMMUNICATION // control signals are coming in via the SUMD interface (comment it out for classic PWM RC signals)

// PPM communication (RX header, 8 channels, working fine, but channel signals are a bit jittery) --------
#define PPM_COMMUNICATION // control signals are coming in via the PPM interface (comment it out for classic PWM RC signals)
```

#### SBUS (recommended, default setting, wired to "SBUS" header, 13 channels)
```
// COMMUNICATION SETTINGS  ********************************************************************************************************************
// Choose the receiver communication mode (never uncomment more than one!) !!! ADJUST THEM BEFORE CONNECTING YOUR RECEIVER AND ESC !!!

// PWM servo signal communication (CH1 - CH4, 35, PPM headers, 6 channels) --------
// PWM mode active, if SBUS, IBUS, and PPM are disabled (// in front of #define)

// SBUS communication (RX header, 13 channels. This is my preferred communication protocol)--------
#define SBUS_COMMUNICATION // control signals are coming in via the SBUS interface (comment it out for classic PWM RC signals)
boolean sbusInverted = false; // false = wired to non standard (inverted) SBUS signal (for example from my "Micro RC" receiver)
uint32_t sbusBaud = 100000; // Standard is 100000. Try to lower it, if your channels are coming in unstable. Working range is about 96000 - 104000.

// IBUS communication (RX header, 13 channels not recommended, NO FAILSAFE, if bad contact in iBUS wiring!) --------
//#define IBUS_COMMUNICATION // control signals are coming in via the IBUS interface (comment it out for classic PWM RC signals)

// SUMD communication (RX header, 12 channels, For Graupner remotes) --------
//#define SUMD_COMMUNICATION // control signals are coming in via the SUMD interface (comment it out for classic PWM RC signals)

// PPM communication (RX header, 8 channels, working fine, but channel signals are a bit jittery) --------
//#define PPM_COMMUNICATION // control signals are coming in via the PPM interface (comment it out for classic PWM RC signals)
```

SBUS non standard signal (if your receiver sends a non-standard SBUS signal):
```
boolean sbusInverted = false; // false = wired to non standard (inverted) SBUS signal (for example from "Micro RC" receiver)
```

SBUS standard signal (default, used in most cases)
```
boolean sbusInverted = true; // false = wired to non standard (inverted) SBUS signal (for example from "Micro RC" receiver)
```

SBUS baudrate fine adjustment. 100000 ist standard. With some receivers, the indicators and other functions may be randomly triggered, because there are bit errors.
This variable allows to fine adjust the baudrate to solve this problem.
```
uint32_t sbusBaud = 100000; // Standard is 100000. Try to lower it, if your channels are coming in unstable. Working range is about 96000 - 104000.
```

#### IBUS (not recommended, NO FAILSAFE, if bad contact in iBUS wiring! "RX" header, 13 channels)
```
// COMMUNICATION SETTINGS **********************************************************************************************
// Choose the receiver communication mode (never uncomment more than one!) !!! ADJUST THEM BEFORE CONNECTING YOUR RECEIVER AND ESC !!!

// PWM servo signal communication (CH1 - CH4, 35, PPM headers, 6 channelschannelSetup.h) --------
// PWM mode active, if SBUS, IBUS, SERIAL and PPM are disabled (// in front of #define)

// SBUS communication (SBUS header, 13 channels. This my preferred communication protocol)--------
//#define SBUS_COMMUNICATION // control signals are coming in via the SBUS interface (comment it out for classic PWM RC signals)
boolean sbusInverted = true; // false = wired to non standard (inverted) SBUS signal (for example from "Micro RC" receiver)

// IBUS communication (RX header, 13 channels not recommended, NO FAILSAFE, if bad contact in iBUS wiring!) --------
#define IBUS_COMMUNICATION // control signals are coming in via the IBUS interface (comment it out for classic PWM RC signals)

// SUMD communication (RX header, 12 channels, For Graupner remotes) --------
//#define SUMD_COMMUNICATION // control signals are coming in via the SUMD interface (comment it out for classic PWM RC signals)

// PPM communication (RX header, 8 channels, working fine, but channel signals are a bit jittery) --------
//#define PPM_COMMUNICATION // control signals are coming in via the PPM interface (comment it out for classic PWM RC signals)
```

#### SUMD (For Graupner remotes "RX" header, 12 channels)
```
// COMMUNICATION SETTINGS  ********************************************************************************************************************
// Choose the receiver communication mode (never uncomment more than one!) !!! ADJUST THEM BEFORE CONNECTING YOUR RECEIVER AND ESC !!!

// PWM servo signal communication (CH1 - CH4, 35, PPM headers, 6 channels) --------
// PWM mode active, if SBUS, IBUS, and PPM are disabled (// in front of #define)

// SBUS communication (SBUS header, 13 channels. This is my preferred communication protocol)--------
//#define SBUS_COMMUNICATION // control signals are coming in via the SBUS interface (comment it out for classic PWM RC signals)
boolean sbusInverted = false; // false = wired to non standard (inverted) SBUS signal (for example from my "Micro RC" receiver)

// IBUS communication (RX header, 13 channels not recommended, NO FAILSAFE, if bad contact in iBUS wiring!) --------
//#define IBUS_COMMUNICATION // control signals are coming in via the IBUS interface (comment it out for classic PWM RC signals)

// SUMD communication (RX header, 12 channels, For Graupner remotes) --------
#define SUMD_COMMUNICATION // control signals are coming in via the SUMD interface (comment it out for classic PWM RC signals)

// PPM communication (RX header, 8 channels, working fine, but channel signals are a bit jittery) --------
//#define PPM_COMMUNICATION // control signals are coming in via the PPM interface (comment it out for classic PWM RC signals)
```

## Adjusting things in "vehicles/yourVehiclePreset.h":
### Shaker
adjust the shaker power for the different engine states to fit your needs:
```
// Shaker parameters (simulating engine vibrations) ---------------------------------------------------------------------
const uint8_t shakerStart = 100; // Shaker power while engine start (max. 255, about 100)
const uint8_t shakerIdle = 49; // Shaker power while idling (max. 255, about 49)
const uint8_t shakerFullThrottle = 40; // Shaker power while full throttle (max. 255, about 40)
const uint8_t shakerStop = 60; // Shaker power while engine stop (max. 255, about 60)
```
### More to come...

## Prototypes:
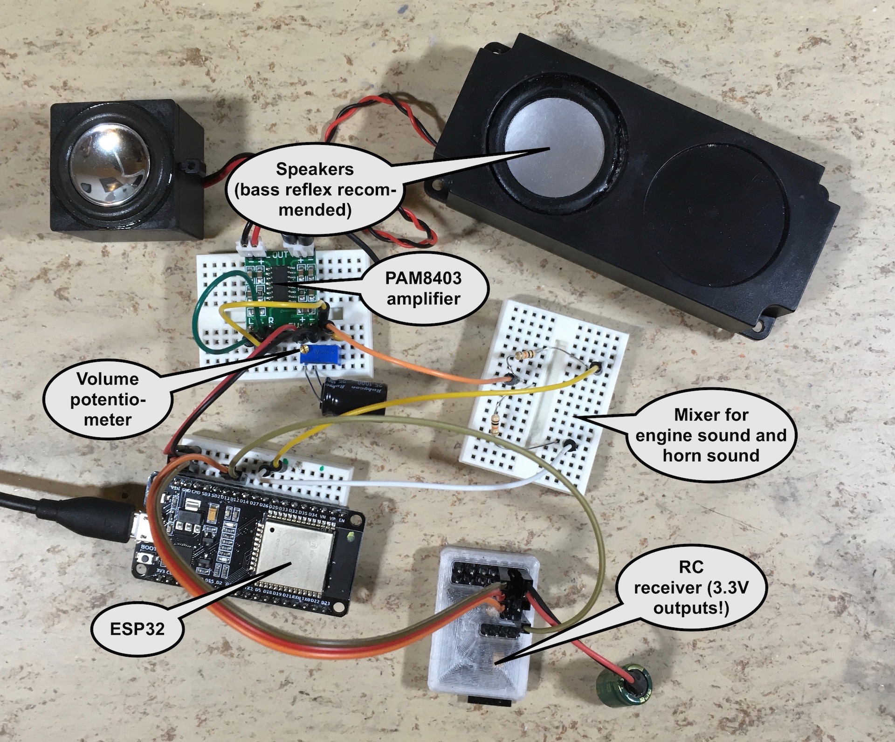
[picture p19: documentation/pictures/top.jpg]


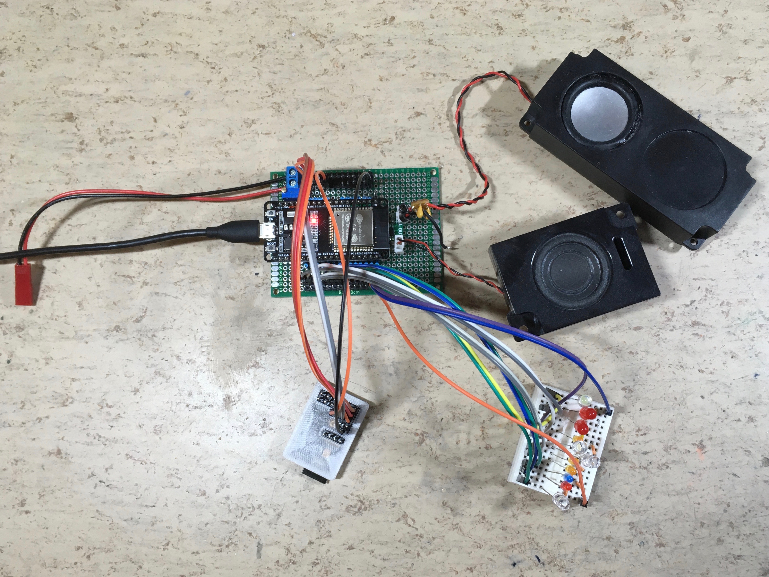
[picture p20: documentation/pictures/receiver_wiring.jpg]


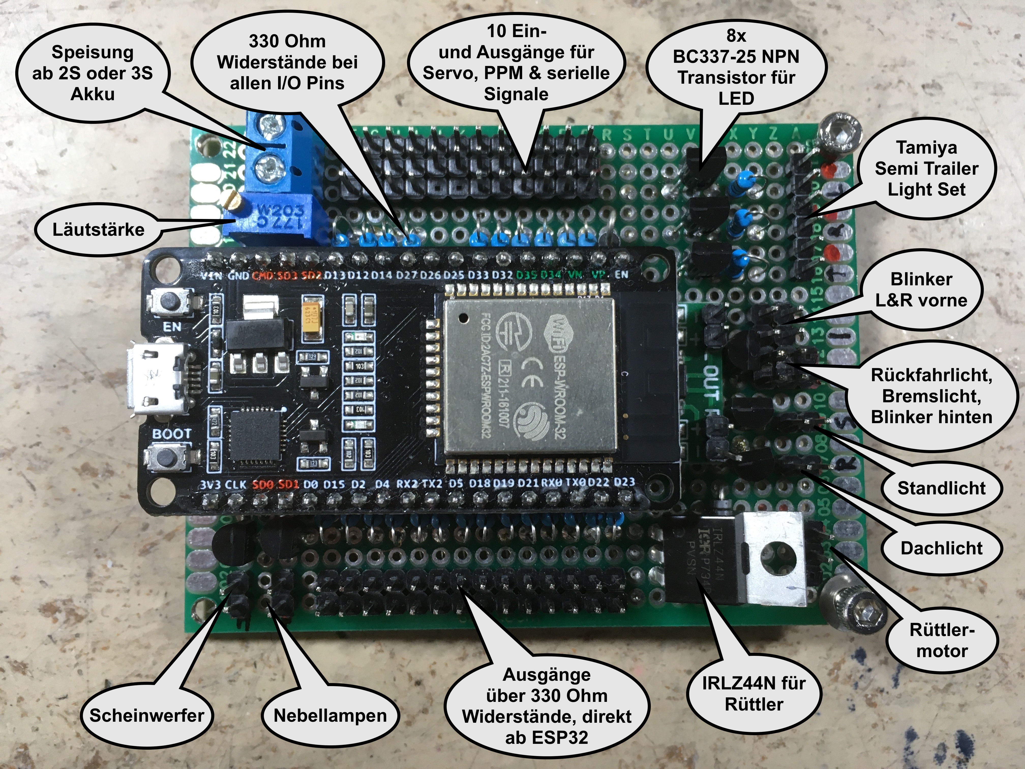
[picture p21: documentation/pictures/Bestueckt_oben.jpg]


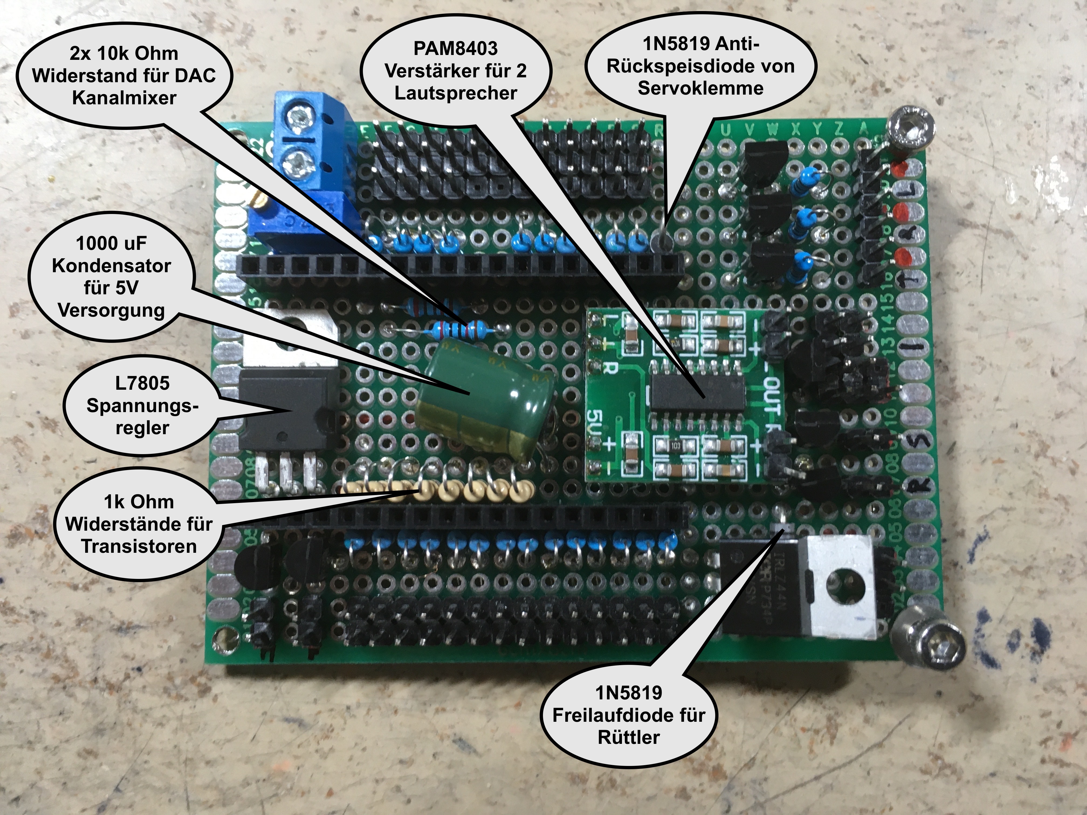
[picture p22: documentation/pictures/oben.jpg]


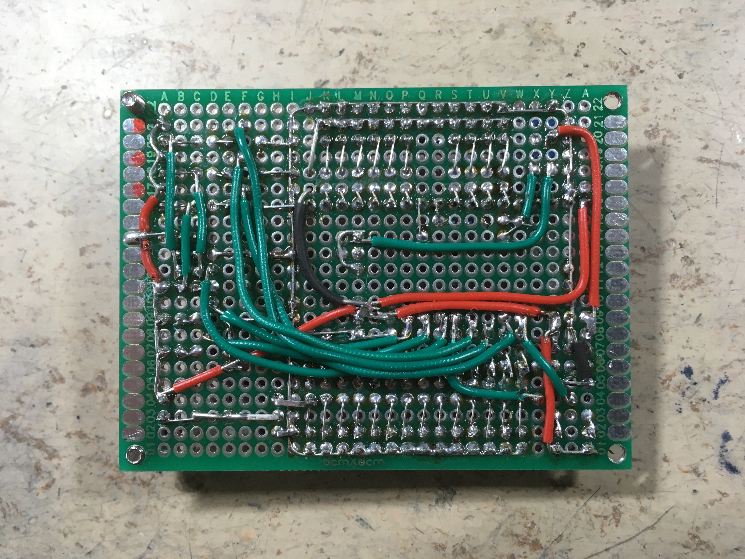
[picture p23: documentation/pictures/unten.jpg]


2019 - 2023, TheDIYGuy999

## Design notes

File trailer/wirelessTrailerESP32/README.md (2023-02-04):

# wirelessTrailerESP32

 The trailer software was moved to: https://github.com/TheDIYGuy999/wirelessTrailerESP32web

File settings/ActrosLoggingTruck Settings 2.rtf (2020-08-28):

/* ******* RECOMMENDED Audacity Settings: 22'050 Hz, 8 bit PCM **********

// Sound files converted with: https://bitluni.net/wp-content/uploads/2018/01/Audio2Header.html
// converter code by bitluni (send him a high five, if you like the code)

Recommended parts & settings for TAMIYA King Hauler:

ESC: HOBBYWING QUICRUN WP Crawler Brushed with the following settings:
1: 3
2: 1
3: 3
4: 3
5: 4
6: 2
7: 9
8: 1
9: 8 (change it, important)
10: 4
11: 4
12: 5
13: 4
14: 1 (be careful here!!)
15: 1 (change it, important)

Motor: 540 size, 35 turns, stock pinion

// ********************************************************************************************************************* */
// Choose the board version
//#define PROTOTYPE_36 // 36 or 30 pin board (do not uncomment it or it will cause boot issues!)

// ---------------------------------------------------------------------------------------------------------------------
// Choose the receiver communication mode (never uncomment more than one! If all commented out = classic PWM RC signal communication)--
// SBUS communication --------
#define SBUS_COMMUNICATION // control signals are coming in via the SBUS interface (comment it out for classic RC signals)

boolean sbusInverted = true; // false = wired to NPN transistor signal inverter or uninverted SBUS signal (for example from "Micro RC" receiver)

// Serial communication --------
//#define SERIAL_COMMUNICATION // control signals are coming in via the serial interface (comment it out for classic RC signals)
// Only for my "Micro RC" receiver! See: https://github.com/TheDIYGuy999/Micro_RC_Receiver

// PPM communication --------
//#define PPM_COMMUNICATION // control signals are coming in via the PPM interface (comment it out for classic RC signals)
#define NUM_OF_CHL 8 // The number of channels inside our PPM signal (usually max. 8)

#define NUM_OF_AVG 1 // Number of averaging passes (usually one, more will be slow)

// Sound files (22'050 Hz, 8 bit PCM recommended) -----------------------------------------------------------------------
// Choose the start sound (uncomment the one you want) --------
volatile int startVolumePercentage = 130; // Adjust the start volume (usually = 100%)
//#include "sounds/UnionPacific2002Start.h" // Union Pacific 2002 SD70M Locomotive Start
//#include "sounds/ScaniaV8Start.h" // Scania V8 Start
//#include "sounds/ScaniaR500V8Start.h" // Scania R500 V8 Start
//#include "sounds/ScaniaV8StartNew.h" // Scania V8 Start
#include "sounds/UralV8Start.h" // Ural 4320 V8 Start (use it for Diesel trucks, if no other is available) use it for King Hauler

//#include "sounds/HgP408Start.h" // HG P408 Humvee Diesel (only for small speakers)
//#include "sounds/DefenderV8Start.h" // Land Rover Defender V8 Start
//#include "sounds/JaguarXjsHeStart.h" // Jaguar XJS HE Starts
//#include "sounds/KenworthW900Start.h" // Kenworth W900 Truck Start
//#include "sounds/MackStart.h" // Mack Truck Start
//#include "sounds/DetroitDieselStart.h" // Detroit Diesel generic Truck Start
//#include "sounds/InternationalDT-466Start.h" // International DT-466 Start
//#include "sounds/Cat3406BStart.h" // Caterpillar 3406B start
//#include "sounds/ActrosV8Start.h" // MB Actros V8 Truck Start
//#include "sounds/VWBeetleStart.h" // VW Beetle or Bug
//#include "sounds/HarleyDavidsonFXSBStart.h" // Harley Davidson FXSB start
//#include "sounds/v8soundteststart.h" // Wombii's Scania V8 Fire Truck start
//#include "sounds/JeepGrandCherokeeTrackhawkStart.h" // Jeep Grand Cherokee Trackhawk start
//#include "sounds/carCranking.h" // Generic car cranking

// Choose the motor idle sound (uncomment the one you want) --------
volatile int idleVolumePercentage = 50; // Adjust the idle volume (usually = 100%, more also working, depending on sound, 50 - 60% if additional diesel knock sound is used)
volatile int engineIdleVolumePercentage = 100; // the engine volume will be throttle dependent (usually = 40%, never more than 100%!)
//#include "sounds/20Hz.h" // 20Hz test tone
//#include "sounds/100Hz.h" // 100Hz test tone
//#include "sounds/1000Hz.h" // 1000Hz test tone
//#include "sounds/UnionPacific2002Idle.h" // Union Pacific 2002 SD70M Locomotive with 16 cylinder Diesel (set volume to 60%)
//#include "sounds/ScaniaV8Idle.h" // Scania V8 (bad quality)
//#include "sounds/ScaniaR500V8Idle.h" // Scania R500 V8
//#include "sounds/ScaniaV8IdleNew.h" // Scania V8 (Volume 100%, 35%, Turbo 70%, 10%, Wastegate 50%, 1%, CEP 100, TSM 2)
//#include "sounds/ScaniaV8IdleNewWarm.h" // Scania V8 (Volume 55%, 40%, Turbo 70%, 10%, Wastegate 200%, 1%, CEP 100, TSM 3, Knock volume 600, 10%, interval 1, 150) the best one!
//#include "sounds/ScaniaR620V8Idle2.h" // Scania R620 V8 (a bit thin, add about 80% turbo volume)
//#include "sounds/ScaniaR620Uphill.h" // Scania R620 V8 going uphill, typical knock - knock under load
//#include "sounds/ScaniaR620Uphill2.h" // Scania R620 V8 going uphill, typical knock - knock under load (this one is better, Volume 180%, 20%, Turbo 60%, 10%, Wastegate 50%, 1%, CEP 100, TSM 2)
//#include "sounds/SCANIAV850TonIdle.h" // 50 ton SCANIA going uphill @ very low rpm (Volume 60%, 40%, Turbo 40%, 10, Wastegate 100%, 1%, CEP 100, TSM 2, Knock volume 600, 0%, interval 4, 50)
//#include "sounds/UralV8Idle.h" // Ural 4320 V8
//#include "sounds/HumveeDieselIdle.h" // "Humvvee" (Hummer H1) V8 Diesel
//#include "sounds/HgP408Idle.h" // HG P408 Humvee Diesel (only for small speakers)
//#include "sounds/DetroitDieselIdle.h" // Detroit Diesel generic Truck (Volume 80%, 30%, Turbo 60%, 10%, Wastegate 50%, 1%, CEP 100, TSM 3)
//#include "sounds/DetroitDieselStraightPipeIdle.h" // Detroit Diesel Truck with straight pipes (use multiplier = 2, acc = 2, dec = 1)
//#include "sounds/DetroitDieselBassBoost15db.h" // Detroit Diesel Truck with straight pipes. Bass 100-200Hz + 15dB
//#include "sounds/DetroitDieselBassBoost7db.h" // Detroit Diesel Truck with straight pipes. Bass 100-200Hz + 7dB (use it for King Hauler, Volume 60%, 40%, Turbo 60%, 10, Wastegate 100%, 1%, CEP 100, TSM 3, Knock volume 400, 10%, interval 2, 50)
//#include "sounds/DetroitDieselPeterbiltCabover.h" // Detroit Diesel Peterbilt cabover truck
//#include "sounds/DetroitDieselKenworth.h" // Detroit Diesel Kenworth truck (use Ural V8 Start & 100% turbo)
//#include "sounds/DetroitDieselJohnDeereTractor.h" // Detroit Diesel John Deere tractor
//#include "sounds/InternationalDT-466Idle.h" // International DT-466 idle (Volume 100%, 35%, Turbo 60%, 10%, Wastegate 30%, 1%, CEP 100, TSM 3)
//#include "sounds/Cat3406BIdle.h" // Caterpillar 3406B idle (Volume 100%, 35%, Turbo 70%, 10%, Wastegate 30%, 1%, CEP 100, TSM 3)
//#include "sounds/M35Idle.h" // AM General M35 Truck
//#include "sounds/M35BassBoost7db.h" // AM General M35 Truck Bass 100-200Hz + 7dB (Volume 100%, 35%, Turbo 100%, 30%)
//#include "sounds/UnimogU1000TurboFullLoad.h" // Unimog U1000 Turbo (Volume 100%, 35%, Turbo 50%, 10%, Wastegate 150%, 1%)
//#include "sounds/ActrosV8Idle.h" // MB Actros V8 Truck Idle (very noisy)
//#include "sounds/ActrosLoggingTruckIdling.h" // Actros logging truck (Volume 80%, 40%, Turbo 60%, 10, Wastegate 100%, 1%, CEP 100, TSM 2, Knock volume 200, 10%, interval 4, 50)
#include "sounds/ActrosLoggingTruckIdling2.h" // Actros logging truck (Volume 50%, 100%, Turbo 10%, 10, Wastegate 100%, 1%, CEP 100, TSM 3, Knock volume 500, 10%, interval 2, 50, ActrosLoggingTruckDieselKnock3.h)

//#include "sounds/KenworthW900Idle.h" // Kenworth W900 Truck Idle (Volume 80%, 30%, Turbo 60%, 10%, Wastegate 50%, 1%, CEP 100, TSM 2)
//#include "sounds/MackIdle.h" // Mack Truck Idle (very thin)
//#include "sounds/Tatra813Idle.h" // Tatra 813 8x8 air cooled V12 Diesel (Volume 80%, 50%, Turbo 0%, 0, Fan 250, 0, 250, No Wastegate, CEP 100, TSM 2, Knock volume 500, 0%, interval 2, 50)
//#include "sounds/DefenderV8Idle.h" // Land Rover Defender V8 (Volume 100%, 40%, Turbo 0%, 0, Fan 0, 0, 250, No Wastegate, CEP 100, TSM 2, Knock volume 500, 0%, interval 2, 50, automatic = true)
//#include "sounds/Mustang68Idle.h" // Ford Mustang 1968
//#include "sounds/DodgeChallenger70Idle.h" // 1970 Dodge Challenger
//#include "sounds/MgBGtV8Idle.h" // MG B GT V8
//#include "sounds/LaFerrariIdle.h" // Ferrari "LaFerrari"
//#include "sounds/chevyNovaV8Idle.h" // Chevy Nova Coupe 1975
//#include "sounds/V8TrophyTruckIdle.h" // V8 Trophy Truck
//#include "sounds/JaguarXjsHeIdle.h" // Jaguar XJS HE (bad quality)
//#include "sounds/VWBeetleIdle.h" // VW Beetle or Bug
//#include "sounds/HarleyDavidsonFXSBIdle.h" // Harley Davidson FXSB (Volume 60%, 40%, Turbo 0%, 10, no Wastegate 100%, CEP 300, TSM 4, Knock volume 300, 10%, interval 2, 50)
//#include "sounds/v8soundtestidle.h" // Wombii's Scania V8 Fire Truck (Volume 90%, 50%, Turbo 20%, 10, Wastegate 90%, 1%, CEP 100, TSM 3, Knock volume 350, 15%, interval 4, 10, ScaniaDieselKnock.h)
//#include "sounds/JeepGrandCherokeeTrackhawkIdle.h" // Jeep Grand Cherokee Trackhawk idle (speaker with good bass required)
//#include "sounds/DAFXFIdle.h" // DAF XF truck

// Choose the motor revving sound (uncomment the one you want) --------
//#define REV_SOUND // uncomment this, if you want to use the separate, optional rev sound
volatile int revVolumePercentage = 150; // Adjust the idle volume (usually = 100%, more also working, depending on sound)
volatile int engineRevVolumePercentage = 30; // the engine volume will be throttle dependent (usually = 40%, never more than 100%!)
const uint8_t revSwitchPoint = 250; // The rev sound is played instead of the idle sound above this point
#ifdef REV_SOUND

//#include "sounds/ScaniaV8Rev.h" // Scania V8
#include "sounds/ScaniaV8Rev2.h" // Scania V8

#endif

// Choose the Diesel (or whatever) ignition "knock" sound (played in the fixed sampling rate interrupt, uncomment the one you want,
// play around here, the results are amazing, if you hit the right combination with the idle sound!) --------
volatile int dieselKnockVolumePercentage = 500; // Adjust the Diesel knock volume (usually = 200 - 600%)
volatile int dieselKnockIdleVolumePercentage = 10; // Diesel knock volume while idling (usually = 20%)
volatile int dieselKnockInterval = 2; // Idle sample length divided by this number (1 - 20, depending on sound files)
volatile int dieselKnockStartPoint = 10; // Volume will raise above this point ( usually 0, for "open pipe" exhaust about 250)
//#define ADAPTIVE_KNOCK_VOLUME // Experimental setting: only the first knock per engine cycle will be full volume!
volatile int dieselKnockAdaptiveVolumePercentage = 50; // Adjust the Diesel knock volume for the non-first knocks per engine cycle (usually = 50%)
//#include "sounds/DieselKnockDummy.h" // If you don't want Diesel knock sound
//#include "sounds/ScaniaR620UphillKnock.h" // Scania R620 V8 (use it for King Hauler)
//#include "sounds/LanzBulldogDieselKnock.h" // Lanz Bulldog tractor (Interval = 2)
//#include "sounds/ScaniaDieselKnock.h" // Strong Scania V8 diesel knock while highway race against Volvo truck (500%, 10%, Interval = 2 possible, for slow running V8 engines)
//#include "sounds/ScaniaDieselKnock2.h" // Strong, short Scania V8 diesel knock while highway race against Volvo truck (Interval = 4 possible, for faster running engines)
//#include "sounds/ScaniaR730V8DieselKnockShort.h" // Hard knock (400%, 0%, Interval = up to 8 possible, for small engines)
//#include "sounds/ScaniaR730V8DieselKnockSlow.h" // Soft knock (500%, 10%, Interval = up to 4 possible, for meduim engines and Scania open pipe (interval = 1))
//#include "sounds/SCANIAV850TonKnock.h" // 50 ton SCANIA knock
//#include "sounds/ActrosLoggingTruckDieselKnock.h" // Actros logging truck
//#include "sounds/ActrosLoggingTruckDieselKnock2.h" // Actros logging truck
#include "sounds/ActrosLoggingTruckDieselKnock3.h" // Actros logging truck (same as idle, for testing)

//#include "sounds/Tatra813Knock.h" // Tatra 813 8x8 air cooled V12 Diesel
//#include "sounds/Tatra813Roar.h" // Tatra 813 8x8 air cooled V12 Diesel (use this for 813)
//#include "sounds/Tatra813RoarShort.h" // Tatra 813 8x8 air cooled V12 Diesel
//#include "sounds/HarleyDavidsonFXSBKnock.h" // Harley Davidson FXSB knock
//#include "sounds/DefenderV8Knock.h" // Land Rover Defender V8 knock (experimental, don't use it)
//#include "sounds/DefenderV8Knock2.h" // Land Rover Defender V8 knock (experimental, don't use it)
//#include "sounds/DefenderV8Knock3.h" // Land Rover Defender V8 knock (experimental, don't use it)
//#include "sounds/DefenderV8Knock4.h" // Land Rover Defender V8 knock (experimental, don't use it)
//#include "sounds/V8TrophyTruckKnock.h" // V8 Trophy Truck
//#include "sounds/chevyNovaV8Knock.h" // Chevy Nova Coupe 1975
//#include "sounds/JeepGrandCherokeeTrackhawkKnock.h" // Jeep Grand Cherokee Trackhawk knock
//#include "sounds/TrackhawkKnock.h" // Jeep Grand Cherokee Trackhawk knock, the more aggressive one!
//#include "sounds/DAFXFKnock.h" // DAF XF truck

// Adjust the additional turbo sound (set "turboVolumePercentage" to "0", if you don't want it) --------
volatile int turboVolumePercentage = 10; // Adjust the turbo volume (usually = 70%)
volatile int turboIdleVolumePercentage = 10; // the turbo volume will be engine rpm dependent (usually = 10%)
#include "sounds/TurboWhistle.h" // Turbo sound, playing in parallel with engine sound!

// Adjust the additional supercharger sound (set "chargerVolumePercentage" to "0", if you don't want it) --------
volatile int chargerVolumePercentage = 0; // Adjust the supercharger volume (usually = 70%)
volatile int chargerIdleVolumePercentage = 10; // the supercharger volume will be engine rpm dependent (usually = 10%)
volatile int chargerStartPoint = 10; // Volume will raise above this point ( usually 10)
#include "sounds/supercharger.h" // supercharger sound, playing in parallel with engine sound!

// Adjust the additional turbo wastegate / blowoff valve sound (set "wastegateVolumePercentage" to "0", if you don't want it)--------
volatile int wastegateVolumePercentage = 100; // Adjust the wastegate volume (usually = 70%, up to 250%)
volatile int wastegateIdleVolumePercentage = 1; // Wastegate sound is played, after rapid throttle drop with engaged clutch
//#include "sounds/WastegateDummy.h"
//#include "sounds/UnimogU1000TurboWastegate.h"
#include "sounds/ScaniaR730V8TurboWastegate.h"

// Adjust the additional cooling fan sound (set "fanVolumePercentage" to "0", if you don't want it) --------
volatile int fanVolumePercentage = 0; // Adjust the fan volume (250% for Tatra 813, else 0%)
volatile int fanIdleVolumePercentage = 0; // the fan volume will be engine rpm dependent (usually = 10%)
volatile int fanStartPoint = 250; // Volume will raise above this point (250 for Tatra 813)
//#include "sounds/Tatra813Fan.h" // Tatra 813 8x8 V12 Diesel Cooling Fan
#include "sounds/Tatra813FanNew.h" // Tatra 813 8x8 V12 Diesel Cooling Fan (use this)

//#include "sounds/Tatra813FanNewSlow.h" // Tatra 813 8x8 V12 Diesel Cooling Fan

// Choose the horn sound (uncomment the one you want) --------
volatile int hornVolumePercentage = 100; // Adjust the horn volume (usually = 100%)
//#include "sounds/TrainHorn.h" // American train horn
//#include "sounds/HornblastersOUTLAWTrainHornLong.h" // Hornblasters outlaw train horn long
//#include "sounds/HornblastersOUTLAWTrainHornShort.h" // Hornblasters outlaw train horn short
#include "sounds/ManTgeHorn.h" // MAN TGE truck horn (King Hauler)

//#include "sounds/westinghouseHorn.h" // American truck horn (the best)
//#include "sounds/FireTruckAirHorn.h" // US fire truck air horn
//#include "sounds/CarHorn.h" // A boring car horn
//#include "sounds/TruckHorn.h" // A generic truck horn
//#include "sounds/PeterbiltHorn.h" // A Peterbilt truck horn
//#include "sounds/2ToneTruckHorn.h" // A 2 tone truck horn

// Choose the siren / additional horn sound (uncomment the one you want) --------
volatile int sirenVolumePercentage = 100; // Adjust the siren volume (usually = 100%)
#include "sounds/sirenDummy.h" // If you don't want siren sound

//#include "sounds/UsPoliceSiren.h" // US Police siren
//#include "sounds/FireTruckAirSiren.h" // US fire truck air siren (King Hauler)
//#include "sounds/FeuerwehrMartinshorn.h" // European Feuerwehr Martinshorn
//#include "sounds/IrishFireEngineHorn.h" // Irish fire truck horn
//#include "sounds/siren01norskere22.h" // Norwegian siren
//#include "sounds/PostAutoHorn.h" // The typical Swiss post bus horn

// Choose the air brake release sound (uncomment the one you want) --------
volatile int brakeVolumePercentage = 150; // Adjust the brake volume (usually = 200%)
//#include "sounds/AirBrakeDummy.h" // If you don't want air brake sound
//#include "sounds/TruckAirBrakes.h" // Short truck air brake sound
//#include "sounds/TruckAirBrakesLong.h" // Long truck air brake sound
#include "sounds/TruckAirBrakes2.h" // Another truck air brake sound

//#include "sounds/AirBrakeSqueak.h" // Squeaky air brake sound

// Choose the parking brake engaging sound (uncomment the one you want) --------
volatile int parkingBrakeVolumePercentage = 150; // Adjust the brake volume (usually = 200%)
//#include "sounds/ParkingBrakeDummy.h" // If you don't want parking brake sound
#include "sounds/ParkingBrake.h" // Parking brake sound

// Choose the gear shifting sound (uncomment the one you want) --------
volatile int shiftingVolumePercentage = 200; // Adjust the shifting volume (usually = 200%)
//#include "sounds/AirShiftingDummy.h" // If you don't want pneumatic shifting sound
//#include "sounds/AirShifting.h" // Pneumatic shifting sound
#include "sounds/ClunkingGearShifting.h" // Manual clunking shifting sound

// Choose the additional "sound1" (uncomment the one you want) --------
volatile int sound1VolumePercentage = 100; // Adjust the sound1 volume (usually = 100%)
//#include "sounds/EMDLocomotiveBell.h" // American EMD locomotive bell
//#include "sounds/007JamesBond.h" // James Bond melody
//#include "sounds/M2Fire.h" // M2 salve
//#include "sounds/GlenCanyon.h" // Glen Canyon country song for truckers ;-)
#include "sounds/door.h" // opening and closing the door

// Choose the reversing beep sound --------
volatile int reversingVolumePercentage = 70; // Adjust the reversing sound volume (usually = 70%)
#include "sounds/TruckReversingBeep.h" // 1000Hz peep sound

// Choose the indicator / turn signal options --------
const boolean indicators = true; // "true", if you want to trigger indicator lights (turn signals)
volatile int indicatorVolumePercentage = 100; // Adjust the indicator sound volume (usually = 100%)
const uint16_t indicatorOn = 300; // The indicator will be switched on above +/- this value, if wheels are turned
const boolean INDICATOR_DIR = true; // adjust indicator direction with true or false
#include "sounds/Indicator.h" // "Tick-Tack" sound

// Choose the blue light options -----------------------------------------------------------------------------------------
const boolean doubleFlashBlueLight = true; // double flash blue lights if "true", "rotating" beacons if "false"

// PWM input signal range calibration ------------------------------------------------------------------------------------
const uint16_t pulseNeutral = 30; // pulseZero +/- this value (30) is the neutral range
const uint16_t pulseSpan = 490; // pulseZero +/- this value (max. 500 or less depending on remote signal range)
const boolean THROTTLE_DIR = false; // adjust throttle direction with true or false

// PWM ESC output signal range calibration (connect crawler type ESC to pin 33)-------------------------------------------
const int16_t escPulseSpan = 1000; // pulseZero +/- this value (> 500 = limited top speed, about 1000 for King Hauler)
const uint8_t escRampTimeFirstGear = 20; // determines, how fast the acceleration and deceleration happens (about 15 - 25, 20 for King Hauler)
const uint8_t escRampTimeSecondGear = 50; // 50 for King Hauler (this value is always in use for automatic transmission, about 80)
const uint8_t escRampTimeThirdGear = 75; // 75 for King Hauler
const uint8_t escBrakeSteps = 30; // determines, how fast the ESC is able to brake down (20 - 30, 30 for King Hauler)
const uint8_t escAccelerationSteps = 3; // determines, how fast the ESC is able to accelerate (2 - 3, 3 for King Hauler)

// Horn trigger signal type (true / false)-------------------------------------------------------------------------------
const boolean pwmSoundTrigger = true; // horn triggered by RC PWM signal instead of constant high level signal, if "true"
// Do NOT enable this boolean, if no PWM signal is connected or you will experience huge engine RPM resopnse delays

// Gearbox parameters (select number of automatic gears in curves.h)-----------------------------------------------------
const boolean automatic = false; // false = linear rpm curve, true = automatic transmission with torque converter is simulated (use it, if you don't have a real shifting transmission)
const boolean doubleClutch = false; // do not activate it at the same time as automatic!
const boolean shiftingAutoThrottle = true; // For Tamiya 3 speed tansmission, throttle is altered for synchronizing, if "true"

// Clutch parameters ---------------------------------------------------------------------------------------------------
uint16_t clutchEngagingPoint = 100; // CEP. The "clutch" is engaging above this point = engine rpm sound in synch with ESC power

// Shaker parameters (simulating engine vibrations) ---------------------------------------------------------------------
const uint8_t shakerStart = 100; // Shaker power while engine start (max. 255, about 100)
const uint8_t shakerIdle = 49; // Shaker power while idling (max. 255, about 49)
const uint8_t shakerFullThrottle = 40; // Shaker power while full throttle (max. 255, about 40)
const uint8_t shakerStop = 60; // Shaker power while engine stop (max. 255, about 60)

// Engine parameters ----------------------------------------------------------------------------------------------------
//Activate for "engine on off" functionality in combination with "Micro RC" Receiver from TheDIYGuy999. No Pulse Zero auto calibration in this case!!
const boolean engineManualOnOff = false;

// Engine RPM range (2 for big Diesels, 4 for fast running motors)
const uint32_t TOP_SPEED_MULTIPLIER = 3; // TSM. RPM multiplier: the bigger the number, the larger the rev range, 2 - 4 is a good place to start. ESP32 will crash, if > 5 @ 22'050Hz!

// Engine mass simulation
const int8_t acc = 2; // Acceleration step (2) 1 = slow for locomotive engine, 9 = fast for trophy truck
const int8_t dec = 1; // Deceleration step (1) 1 = slow for locomotive engine, 5 = fast for trophy truck

// Vehicle type ----------------------------------------------------------------------------------------------------
// #define CATERPILLAR_MODE // For Tanks, diggers, excavators etc. which use dual throttle input on CH2 and CH3

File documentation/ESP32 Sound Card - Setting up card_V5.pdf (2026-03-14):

# ESP32 RC Sound & Light Controller

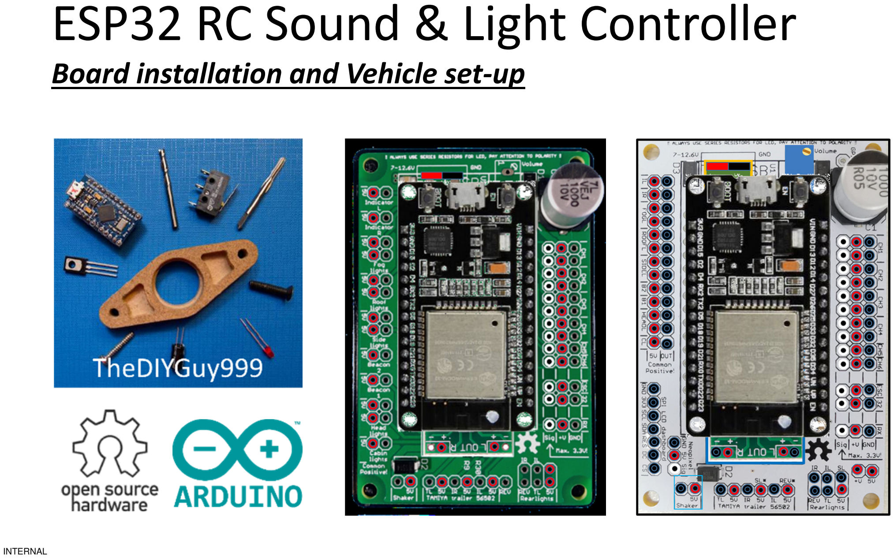
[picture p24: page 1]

INTERNAL

## Board installation and Vehicle set-up

INTERNAL

# ESP32 RC Sound & Light Controller

Safety Regulations

This product must not be used until this manual has been fully read and understood. Likewise, you must agree with all the restrictions mentioned in this section.

- This open source product is left to the user's own responsibility for use, free development and customization. TheDIYGuy999 assumes no liability whatsoever for any damage or consequential damage resulting from the use of this system.
- This product is not suitable for large and dangerous models, because there is no redundancy.
- Never use this product on public roads.
- This product has not been tested for FCC or CE compliance.
- Never connect or disconnect wires while the product is connected to a battery.
- Always disconnect the battery, when this product is not in use. It always draws a couple of Milliamps, even if the ESC is switched off and will drain the battery otherwise!
- This product is not protected against wrong polarity! Always double check your wiring before connecting the battery. Wrong polarity will immediately destroy the product.
- Always insulate the vehicle wiring properly, using heat shrinks in order to prevent short circuits. Never mount the bare PCB directly on top of a metal plate. This will cause short circuits.
- This product may only be used in dry locations.
- This product is not suitable for children below 14 years.

Source: TheDIYGUY999 Quick start manual

INTERNAL

# ESP32 RC Sound & Light Controller

LED Wiring

The LED supply voltage is 5V, coming from the internal regulator. A common LED maximum current is 15mA. The following chart provides the required minimum series resistor Values.

- You can also use a calculator in order to determine the correct value: https://www.digikey.de/en/resources/conversion-calculators/conversion-calculator-led-series-resistor

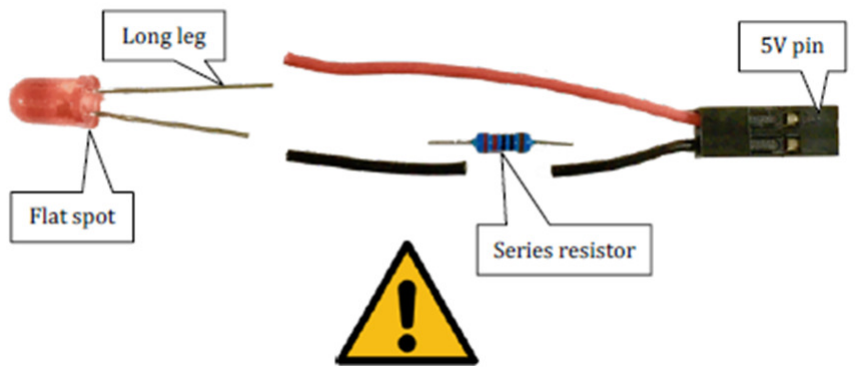
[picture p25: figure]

Source: TheDIYGUY999 Quick start manual

LED color | Forward voltage [Volts] | Minimum resistor [Ohms]
Red | 1.8 | 220
Orange | 1.9 | 220
Green | 2 | 200
White | 3 | 150
Blue | 3 | 150

INTERNAL

# ESP32 RC Sound & Light Controller

LED Wiring

- The LED will not light up, if connected the wrong way around.
- Never connect LED or other devices without a suitable series resistor to the LED output pins (except the TAMIYA trailer connector). This will permanently damage the integrated ULN2003 LED drivers.
- If more than one LED is wired in parallel to an LED output pin, each one needs its own series resistor.
- Two red or orange LED can be wired in series. This makes the circuit more efficient. In this case you need to add both series voltages together for the series resistor calculation.
- The maximum average LED output current per channel is 100mA. However, it is not recommended to load each channel with this current. Otherwise, the ULN2003 LED driver may overheat. Always check it for excessive temperature raise for at least 10 minutes after you wired a new vehicle. If the temperature is too high to the touch, you should use an external driver transistor for the LED.
- Also note, that the maximum sum current for the entire 5V rail, which is supplied by the on-board regulator is 1A.

Source: TheDIYGUY999 Quick start manual

# ESP32 RC Sound & Light Controller

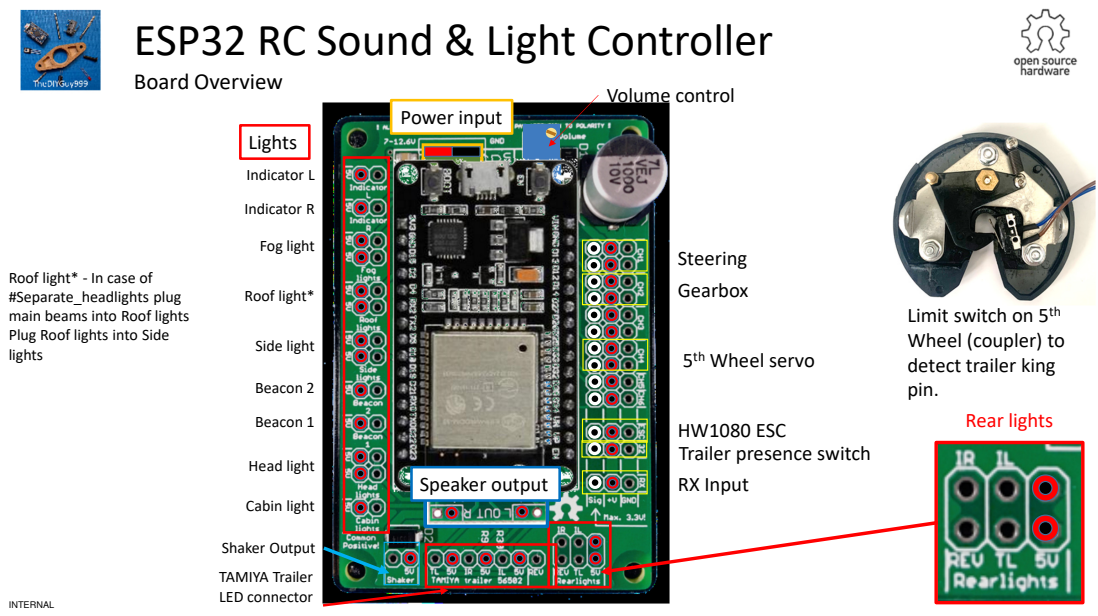
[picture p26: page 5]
INTERNAL; Board Overview; Steering; Gearbox; Lights; Power input; Indicator L; Indicator R; Fog light; Roof light*; Side light; Beacon 2; Beacon 1; Head light; Cabin light; TAMIYA Trailer LED connector; Shaker Output; 5th Wheel servo; Rear lights; Speaker output; Volume control

Roof light* - In case of
#Separate_headlights plug
main beams into Roof lights
Plug Roof lights into Side
lights

Limit switch on 5th
Wheel (coupler) to
detect trailer king
pin.

HW1080 ESC
Trailer presence switch
RX Input

# ESP32 RC Sound & Light Controller

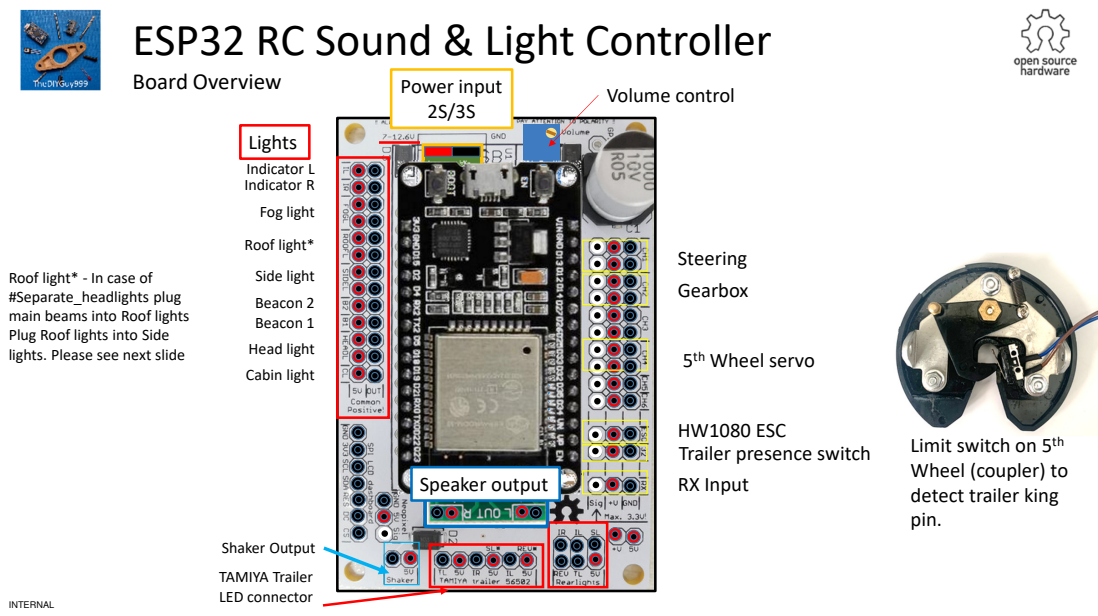
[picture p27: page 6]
INTERNAL; Board Overview; Steering; Gearbox; RX Input; HW1080 ESC; Lights; Power input 2S/3S; Indicator L Indicator R; Fog light; Roof light*; Side light; Beacon 2 Beacon 1; Head light; Cabin light; TAMIYA Trailer LED connector; Shaker Output; 5th Wheel servo; Trailer presence switch; Limit switch on 5th Wheel (coupler) to; Speaker output; Volume control

Roof light* - In case of
#Separate_headlights plug
main beams into Roof lights
Plug Roof lights into Side
lights. Please see next slide

detect trailer king
pin.

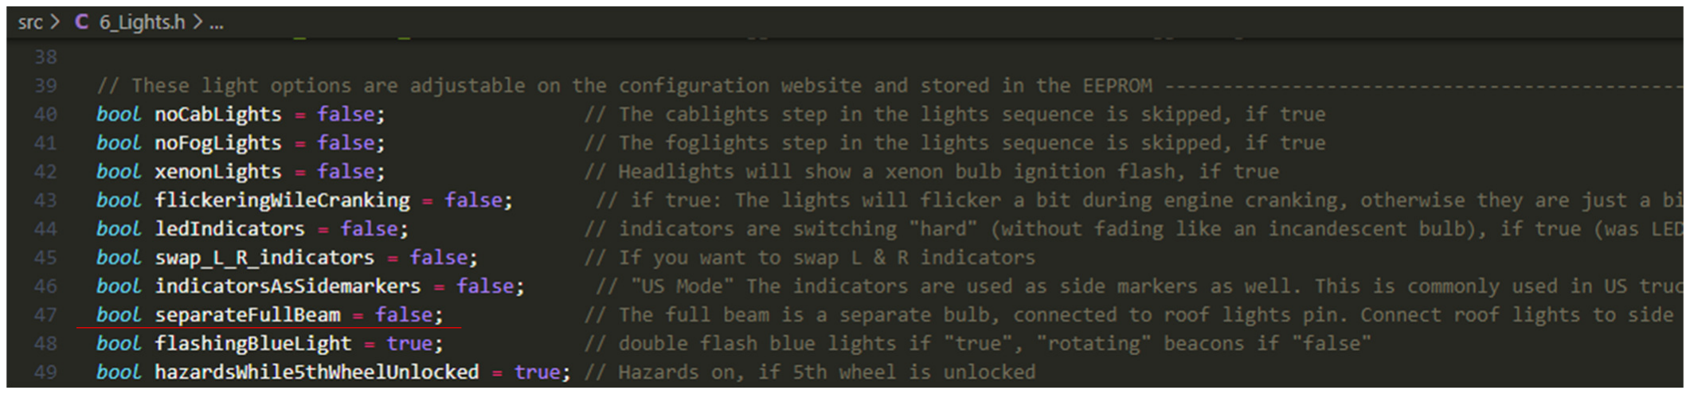
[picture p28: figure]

INTERNAL

# ESP32 RC Sound & Light Controller

6_Lights.h

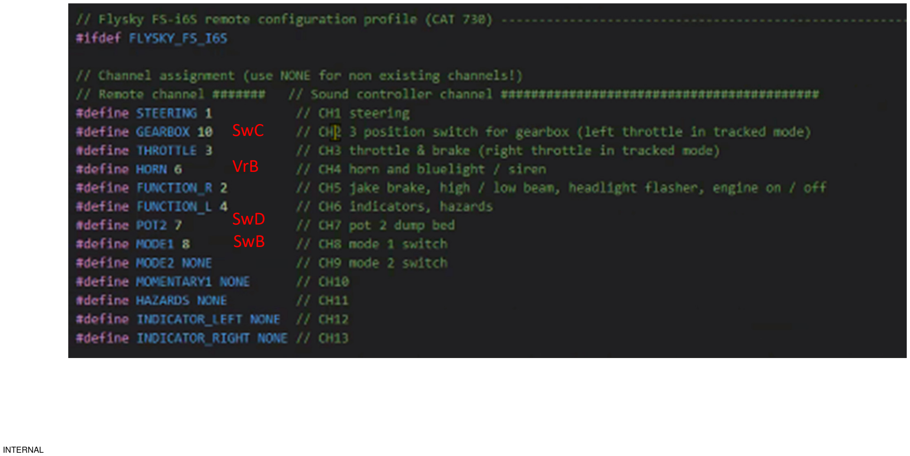
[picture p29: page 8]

INTERNAL

SwC

VrB

SwD
SwB

# ESP32 RC Sound & Light Controller

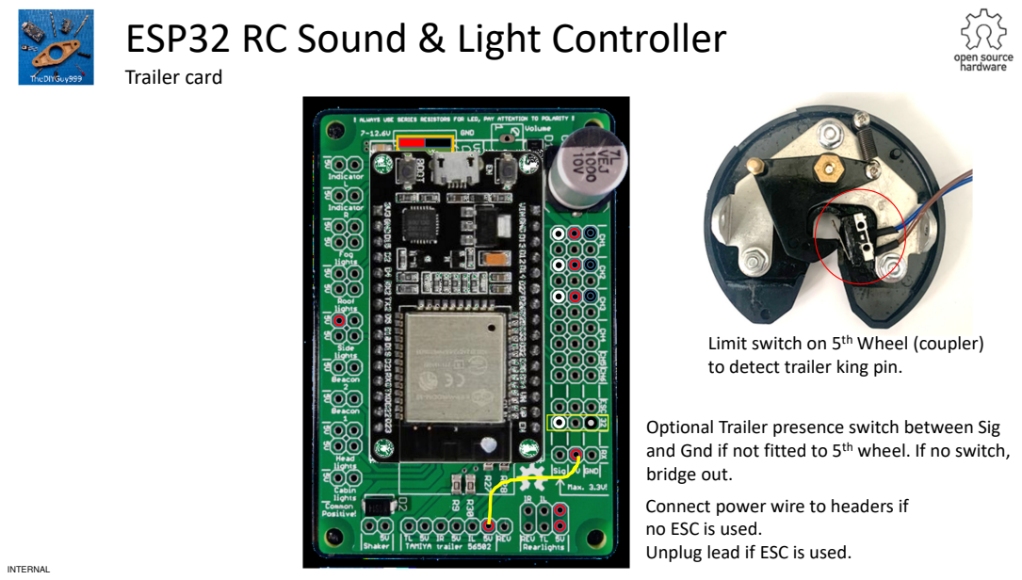
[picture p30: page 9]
INTERNAL; Trailer card

Limit switch on 5th Wheel (coupler)
to detect trailer king pin.

Optional Trailer presence switch between Sig
and Gnd if not fitted to 5th wheel. If no switch,
bridge out.
Connect power wire to headers if
no ESC is used.
Unplug lead if ESC is used.

# ESP32 RC Sound & Light Controller

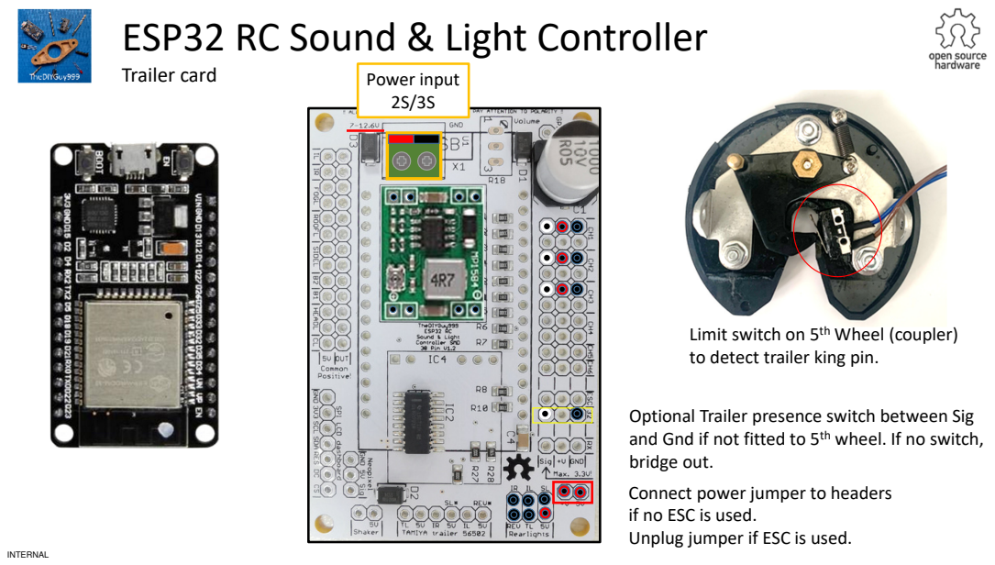
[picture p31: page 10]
INTERNAL; Trailer card; Power input 2S/3S

Limit switch on 5th Wheel (coupler)
to detect trailer king pin.

Optional Trailer presence switch between Sig
and Gnd if not fitted to 5th wheel. If no switch,
bridge out.
Connect power jumper to headers
if no ESC is used.
Unplug jumper if ESC is used.

INTERNAL

# ESP32 RC Sound & Light Controller

Hobbywing 1080 ESC setup

Set up your HW1080 prior to connecting to the Sound Card.
Ensure the throttle is calibrated. (plug ESC into RX Ch3 and set points)

https://youtu.be/RRYwr14FwjE

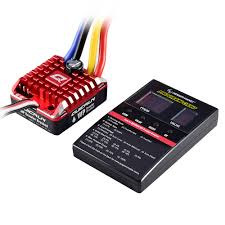
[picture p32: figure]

INTERNAL

# ESP32 RC Sound & Light Controller

Hobbywing 1080 ESC setup

Program the ESC with the program card

Item: | Value
1: | 3
2: | 1 (1= LiPo, 2 = NIMH battery)
3: | 3
4: | 3
5: | 4
6: | 2
7: | 9
8: | 1
9: | 8 (change it, important)
10: | 4
11: | 4
12: | 5
13: | 5 (16KHz = less whining)
14: | 1 (be careful here, this will change the BEC voltage!!)
15: | 1 (change it, important)

# ESP32 RC Sound & Light Controller

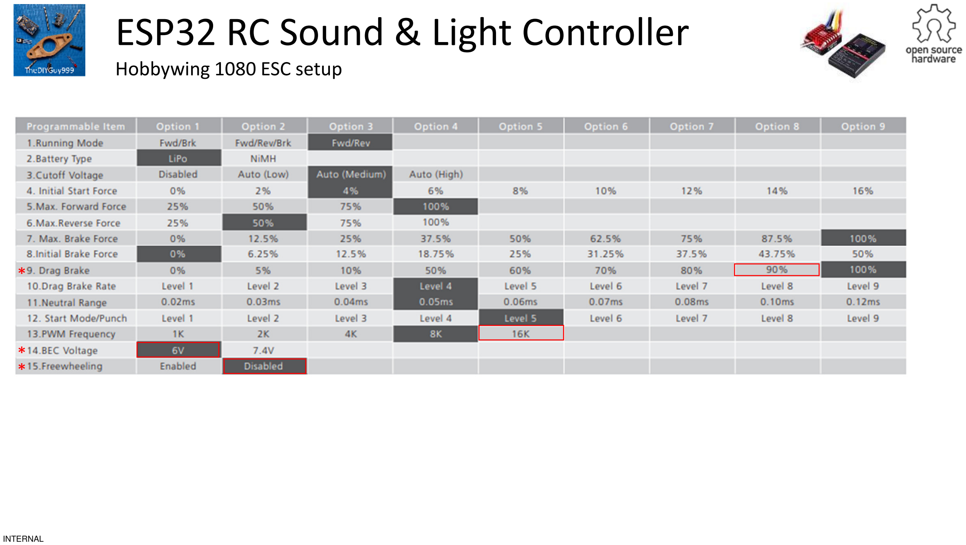
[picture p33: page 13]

INTERNAL

Hobbywing 1080 ESC setup

*

*

*

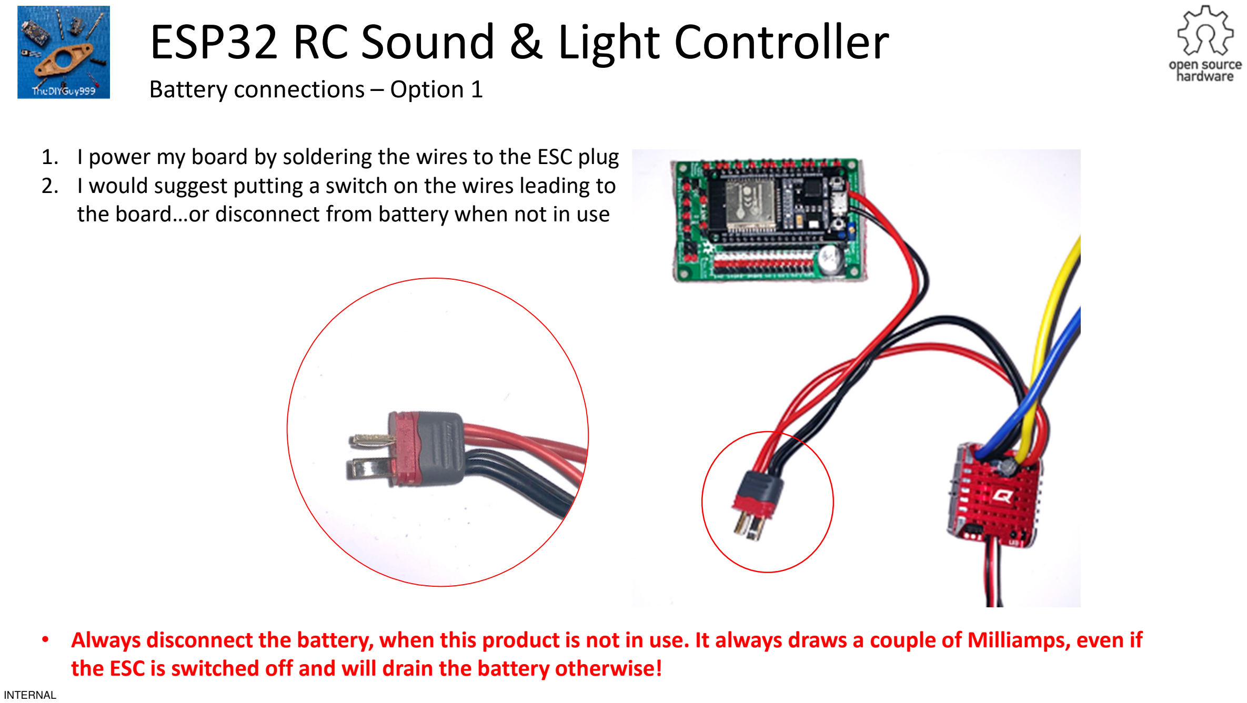
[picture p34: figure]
INTERNAL; ESP32 RC Sound & Light Controller; Battery connections – Option 1

### 1. I power my board by soldering the wires to the ESC plug 2. I would suggest putting a switch on the wires leading to

the board…or disconnect from battery when not in use

- Always disconnect the battery, when this product is not in use. It always draws a couple of Milliamps, even if the ESC is switched off and will drain the battery otherwise!

# ESP32 RC Sound & Light Controller

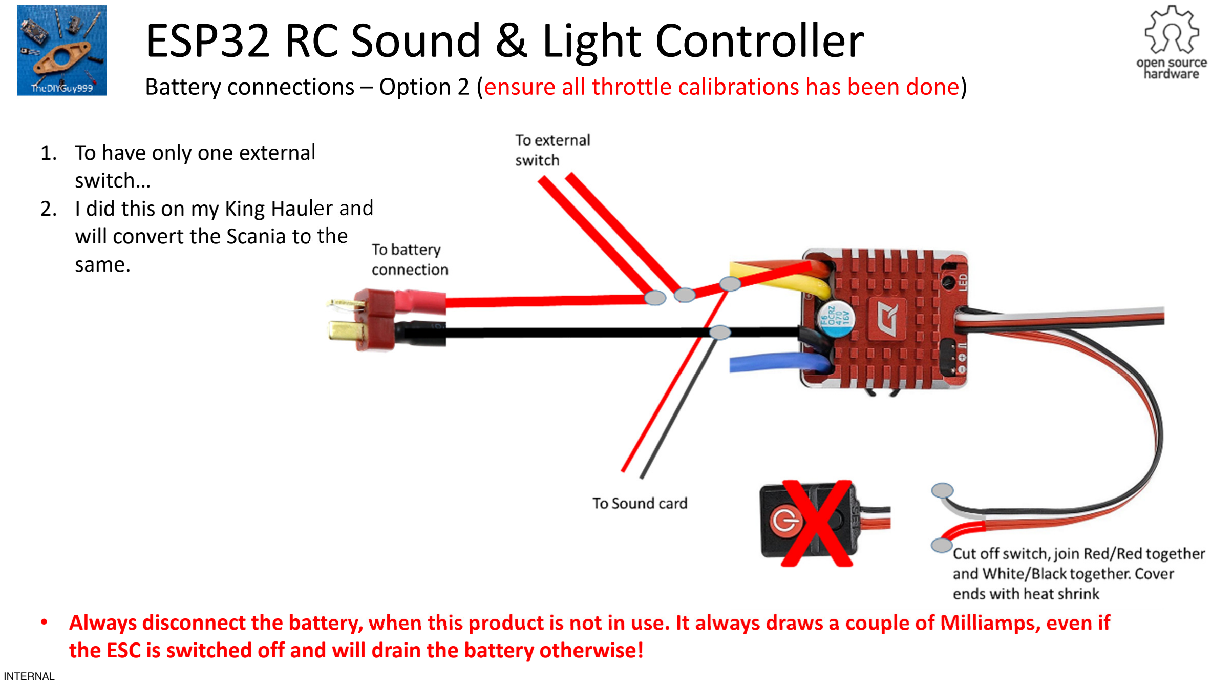
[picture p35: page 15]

INTERNAL

Battery connections – Option 2 (ensure all throttle calibrations has been done)

### 1. To have only one external

switch…

### 2. I did this on my King Hauler and

will convert the Scania to the same.

- Always disconnect the battery, when this product is not in use. It always draws a couple of Milliamps, even if the ESC is switched off and will drain the battery otherwise!

INTERNAL

# ESP32 RC Sound & Light Controller

Receiver connection

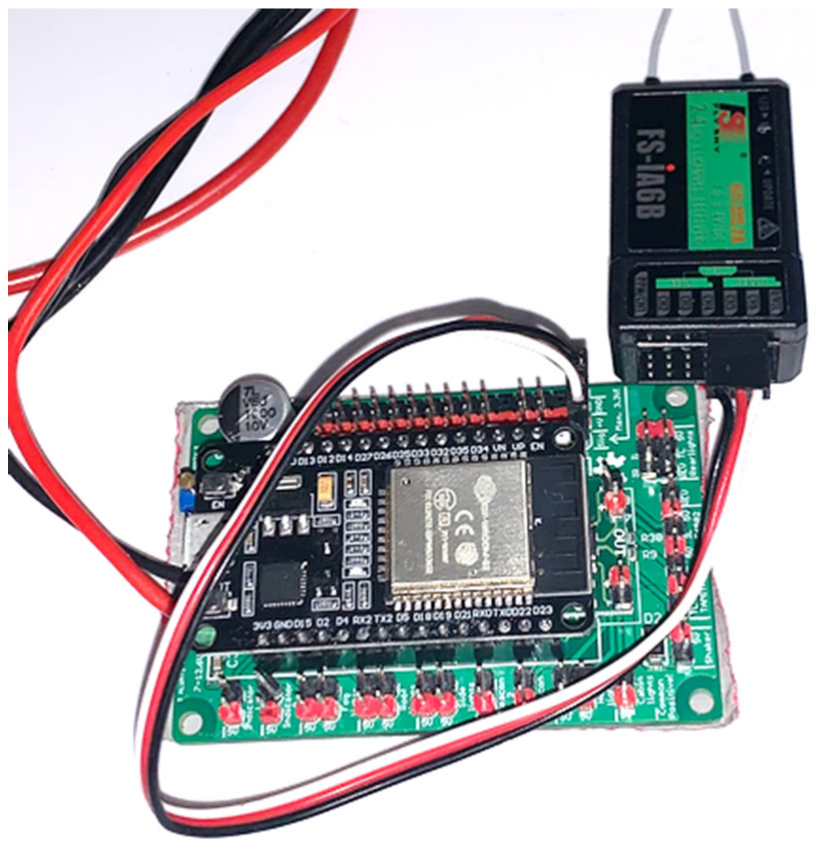
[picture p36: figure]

### 1. If IBUS or SBUS communication is selected, only one

wire is needed from the receiver to the Sound Card

INTERNAL

# ESP32 RC Sound & Light Controller

Flysky FS-i6X modified setup to free up Pot A “VrA” to Ch6 - control other electronic function

PWM | PPM | SBUS | IBUS

Remote
channel | Name | Direction | Duration | Switch A up (100% DR) | Switch A down (75% DR)
1 | STEERING | 1 | Stick horizontal right
2 | GEARBOX | 8 | Switch C (3 pos.)
3 | THROTTLE | 3 | Stick vertical left
4 | HORN | 5 | Pot B "VrB"
| | | togggle long | High / low beam | light state up
toggle
momentary | Headlights flasher
down | togggle long | volume (1 | Engine on / off
| toggle
| momentary | Jakebrake
togggle long | hazards
toggle | left indicator on / off
momentary
right | togggle long | | 5th wheel unlocking (3
| toggle | right indicator on / off
| momentary
7 | POT A | 6 | Pot A "VrA"
8 | MODE1 | 7 | Switch D
9 | MODE2 | 9 | Switch B
momentary | 10 | MOMENTARY1 | 16
11 | HAZARDS | 16
12 | INDICATOR_LEFT | 16
13 | INDICATOR_RIGHT | 16

Type

Sound
controller
channel

Name

Yes, CH1 - CH4, 35, PPM *

Yes, RX

Yes, SBUS
Yes, RX

analog or 3
position
ESP32 sound controller | FLYSKY FS-i6X (with lightbar)

Steering
Gearbox shifting
Throttle & brake
Joystick, button, potentiometer | Function

Horn, bluelight & siren

### 5 FUNCTION_R

### 2 Stick vertical right

up

Transmission neutral (2

No

Stick horizontal left

left

### 6 FUNCTION_L

4

not available
not available

Sound 1
not available (Switch A internally used for DR)

flags

not available

No

Lightbar (connect to CH6 on Flysky RX) latching 2
position

INTERNAL

# ESP32 RC Sound & Light Controller

Flysky FS-i6X Standard setup

Usable with, Header: | Type | Sound controller channel | Name | Joystick, button, potentiometer | Function
PWM | PPM | SBUS | IBUS | | | | Remote channel | Name | Direction | Duration | Switch A up (100% DR) | Switch A down (75% DR)
| | | | | 1 | STEERING | 1 | Stick horizontal right | | | Steering
| | | | | 2 | GEARBOX | 6 | Switch C (3 pos.) | | | Gearbox shifting
| | | | | 3 | THROTTLE | 3 | Stick vertical left | | | Throttle & brake
| | | | | 4 | HORN | 5 | Pot B "VrB" | | | Horn, bluelight & siren
| | | | | 5 | FUNCTION_R | 2 | Stick vertical right | up | togggle long | High / low beam | light state up
| | | | | | | | | | toggle
| | | | | | | | | | momentary | Headlights flasher
| | | | | | | | | down | togggle long | volume (1 | Engine on / off
| | | | | | | | | | toggle
| | | | | | | | | | momentary | Jakebrake
| | | | | 6 | FUNCTION_L | 4 | Stick horizontal left | left | togggle long | | hazards
| | | | | | | | | | toggle | left indicator on / off
| | | | | | | | | | momentary
| | | | | | | | | right | togggle long | | 5th wheel unlocking (3
| | | | | | | | | | toggle | right indicator on / off
| | | | | | | | | | momentary
| | | | | 7 | POT2 | 8 | Pot A "VrA" | | | not used
| | | | latching 2 position | 8 | MODE1 | 7 | Switch D | | | Transmission neutral (2
| | | | | 9 | MODE2 | 9 | Switch B | | | Sound 1
| | | | momentary | 10 | MOMENTARY1 | 16 | | | | not available (Switch A internally used for DR)
| | | | flags | 11 | HAZARDS | 16 | | | | not available
| | | | | 12 | INDICATOR_LEFT | 16 | | | | not available
| | | | | 13 | INDICATOR_RIGHT | 16 | | | | not available

ESP32 sound controller

Yes, CH1 - CH4, 35, PPM *

Yes, RX

Yes, SBUS
Yes, RX

No

No

analog or 3
position

FLYSKY FS-i6X

INTERNAL

# ESP32 RC Sound & Light Controller

Flysky FS-i6X modified setup to use Pot A “VrA” to control “other”

Modified code on Remote Tab

// Channel assignment (use NONE for non existing channels!)
// Remote channel ####### // Sound controller channel ##################################
#define STEERING 1 | // CH1 steering

//#define GEARBOX 6 | // CH2 3 position switch for gearbox (left throttle in tracked mode)
#define GEARBOX 8 | // CH2 3 position switch for gearbox (left throttle in tracked mode)

#define THROTTLE 3 | // CH3 throttle & brake (right throttle in tracked mode)

#define HORN 5 | // CH4 horn and bluelight / siren

#define FUNCTION_R 2 | // CH5 jake brake, high / low beam, headlight flasher, engine on / off

#define FUNCTION_L 4 | // CH6 indicators, hazards

//#define POT2 8 | // CH7 pot 2
#define POT2 6 | // CH7 pot 2

#define MODE1 7 | // CH8 mode 1 switch

#define MODE2 9 | // CH9 mode 2 switch

#define MOMENTARY1 NONE | // CH10

#define HAZARDS NONE | // CH11

#define INDICATOR_LEFT NONE | // CH12

#define INDICATOR_RIGHT NONE | // CH13

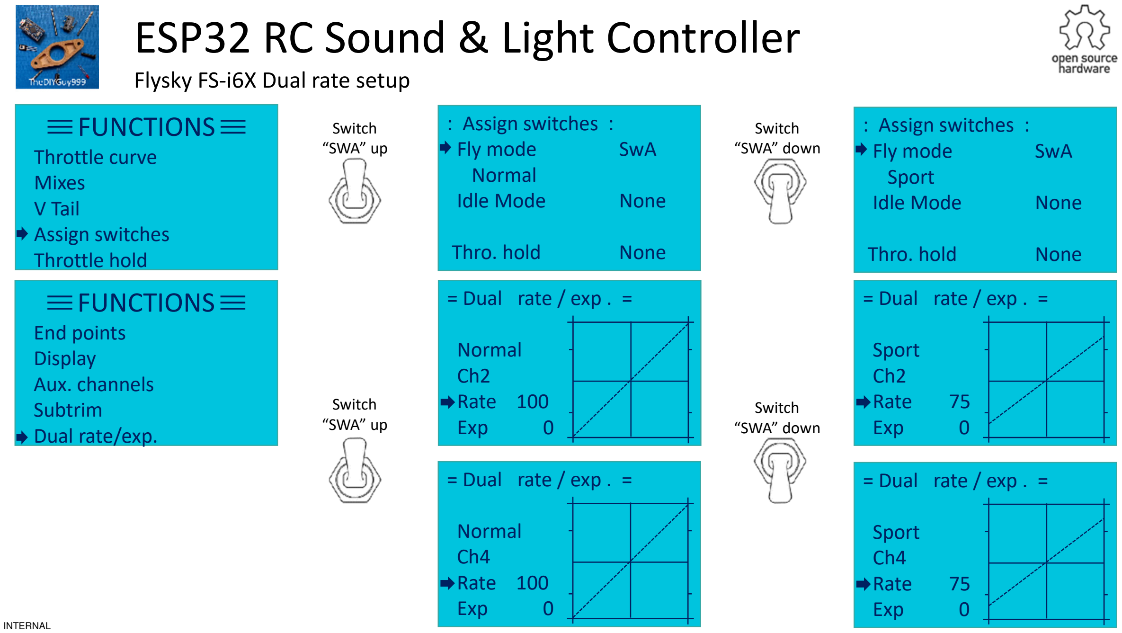
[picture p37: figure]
INTERNAL; = Dual rate / exp . =; Sport Ch2; Rate; Exp; Normal Ch2 Rate 100; Sport Ch4; Normal Ch4 Rate 100; FUNCTIONS; Throttle curve Mixes V Tail Assign switches Throttle hold; : Assign switches :; Fly mode; SwA; Normal; Idle Mode; None; Thro. hold; Sport; Switch “SWA” up; Switch “SWA” down; End points Display Aux. channels Subtrim Dual rate/exp.; ESP32 RC Sound & Light Controller; Flysky FS-i6X Dual rate setup

INTERNAL

Aux . Channels
Channel 5
Source VrB

Channel 8
Source VrA

Aux . Channels
Channel 7
Source SwD

Channel 6
Source SwC

Aux . Channels
Channel 9
Source SwB

Channel 10
Source None

Horn/Beacon lights / trailer control

External – plug into Rx Ch 6 (e.g. control light switch)

Virtual neutral (rev truck)

### 3 position Gear shift

Un-couple 5th wheel servo (trailer control)

### FUNCTIONS

End points
Display
Aux. channels
Subtrim
Dual rate/exp.

# ESP32 RC Sound & Light Controller

Flysky FS-i6X standard setup

INTERNAL

Aux . Channels
Channel 5
Source VrB

Channel 6
Source VrA

Aux . Channels
Channel 7
Source SwD

Channel 8
Source SwC

Aux . Channels
Channel 9
Source SwB

Channel 10
Source None

Horn/Beacon lights / trailer control

External – plug into Rx Ch 6 (e.g. control light switch)

Virtual neutral (rev truck)

### 3 position Gear shift

Un-couple 5th wheel servo (trailer control)

### FUNCTIONS

End points
Display
Aux. channels
Subtrim
Dual rate/exp.

# ESP32 RC Sound & Light Controller

Flysky FS-i6X modified setup

# ESP32 RC Sound & Light Controller

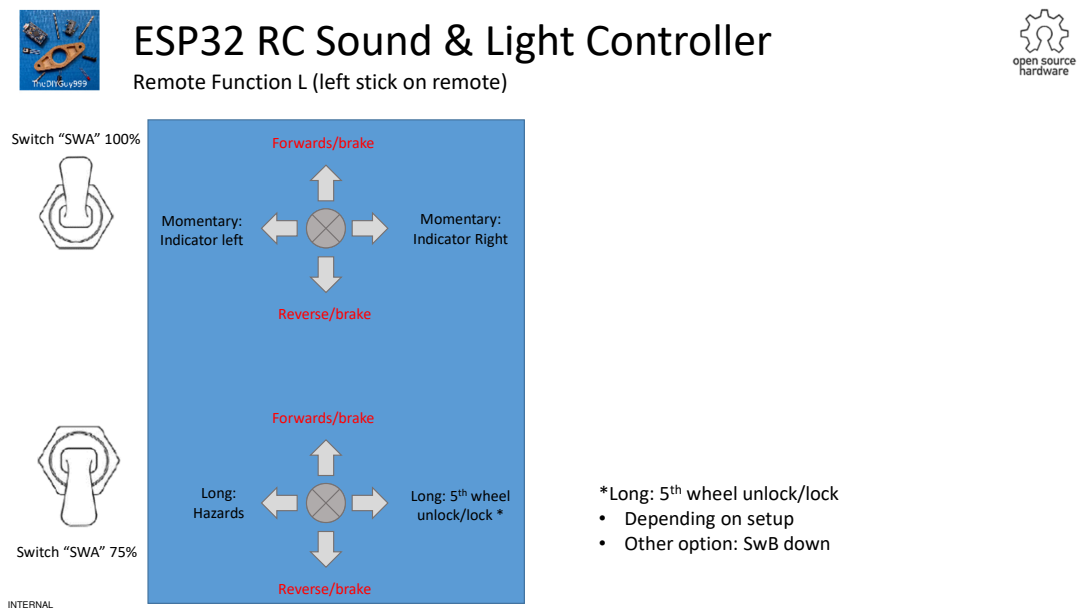
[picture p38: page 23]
INTERNAL; Momentary: Indicator left; Momentary: Indicator Right; Forwards/brake; Reverse/brake; Long: Hazards; Long: 5th wheel unlock/lock *; Switch “SWA” 100%; Switch “SWA” 75%

Remote Function L (left stick on remote)

*Long: 5th wheel unlock/lock
• Depending on setup
• Other option: SwB down

# ESP32 RC Sound & Light Controller

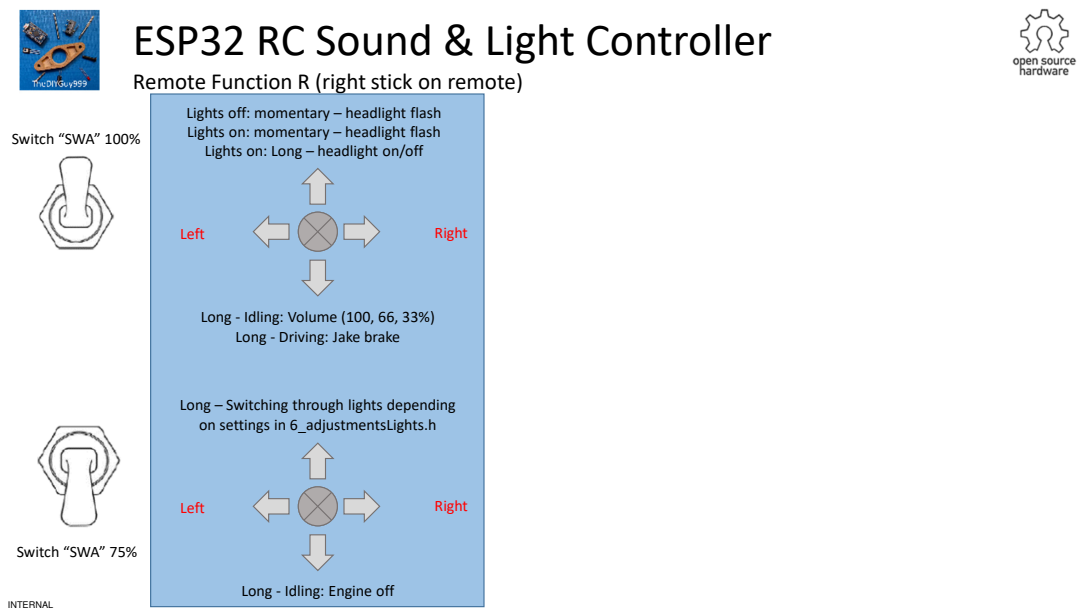
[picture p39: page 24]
INTERNAL; Switch “SWA” 100%; Switch “SWA” 75%; Left; Right

Remote Function R (right stick on remote)

Lights off: momentary – headlight flash
Lights on: momentary – headlight flash
Lights on: Long – headlight on/off

Long - Idling: Volume (100, 66, 33%)
Long - Driving: Jake brake

Long – Switching through lights depending
on settings in 6_adjustmentsLights.h

Long - Idling: Engine off

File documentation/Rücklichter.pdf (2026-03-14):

Verdrahtung Rücklichter

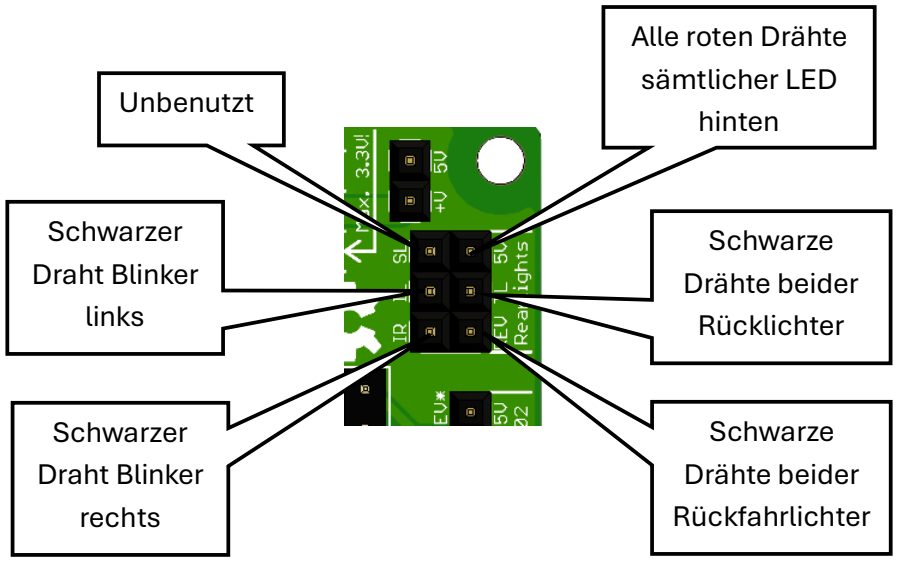
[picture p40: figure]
Unbenutzt; Alle roten Drähte sämtlicher LED hinten; Schwarze Drähte beider Rücklichter; Schwarze Drähte beider Rückfahrlichter; Schwarzer Draht Blinker links; Schwarzer Draht Blinker rechts

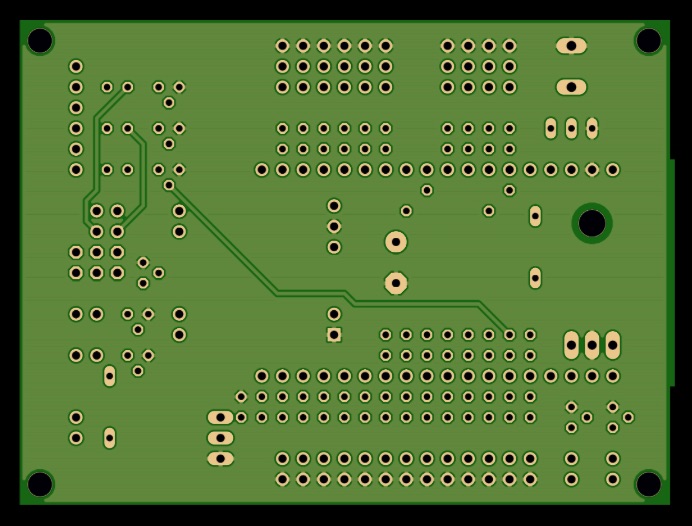
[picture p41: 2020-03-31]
documentation/pictures/pcbBottom.jpg

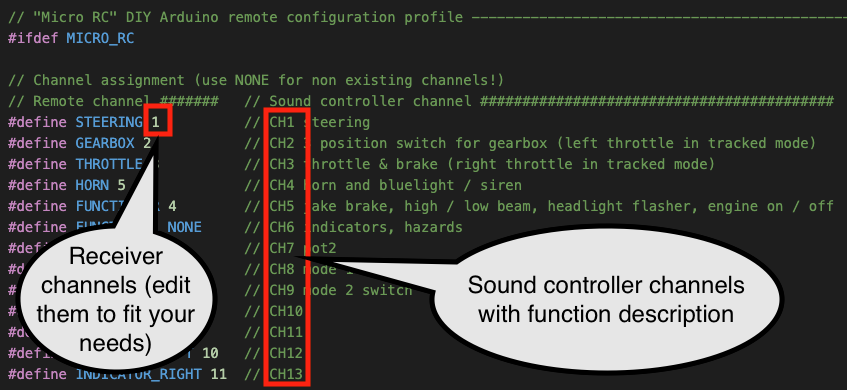
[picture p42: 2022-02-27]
documentation/pictures/CH_Mapping.png

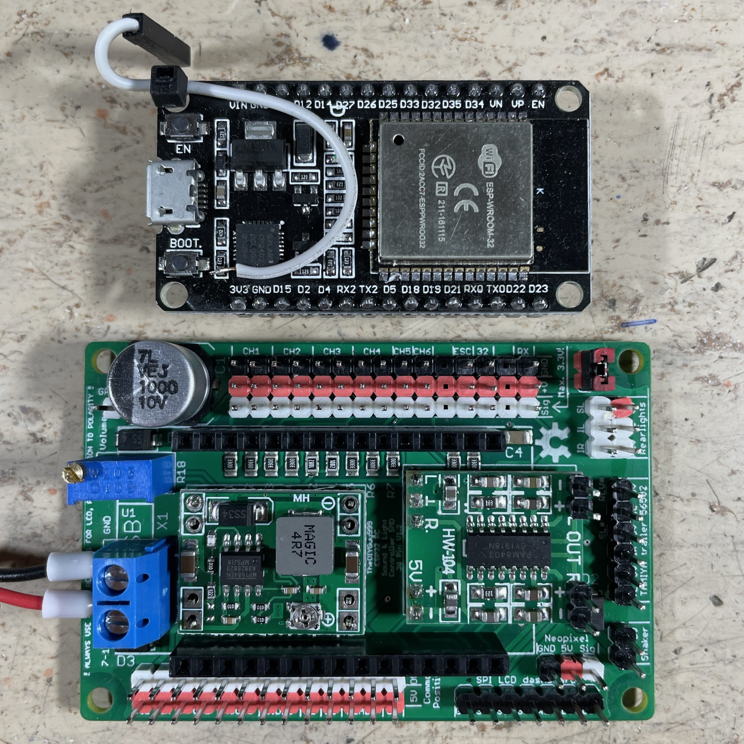
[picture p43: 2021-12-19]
documentation/pictures/30pinSmdSwitchModeVersion.jpg

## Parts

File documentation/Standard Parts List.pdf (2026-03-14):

TheDIYGuy999 | ESP32 Sound and Light Controller SMD V1.2 | Pre assembled PCB and required additional components for finalization
Item number | Pcs. | Name | Type | Picture | Supplier link | Comment
1 | | ESP32 Sound and Light Controller SMD V1.2 | Version 1.2 with switch mode power supply and dashboard connector. | | https://www.pcbway.com/project/shareproject/Arduino_RC_engine_sound_light_controller_for_ESP32_a9334731.html | Select "PCB+ Assembly" (All SMD components will already be soldered), then "Add to Cart"
2 | 1 | 2.54 mm Male Pin Header | 10 PCS, 1x40 Pin black | | https://de.aliexpress.com/item/1005005258694395.html
3 | 1 | | 10 PCS, 1x40 Pin white
4 | 1 | | 10 PCS, 1x40 Pin red
5 | | 2.54 mm Female Header | 20PCS, 15 Pins | | https://de.aliexpress.com/item/4000278469653.html
6 | 1 | Terminal Block | 10 PCS, 2P blue | | https://de.aliexpress.com/item/1005006642865467.html

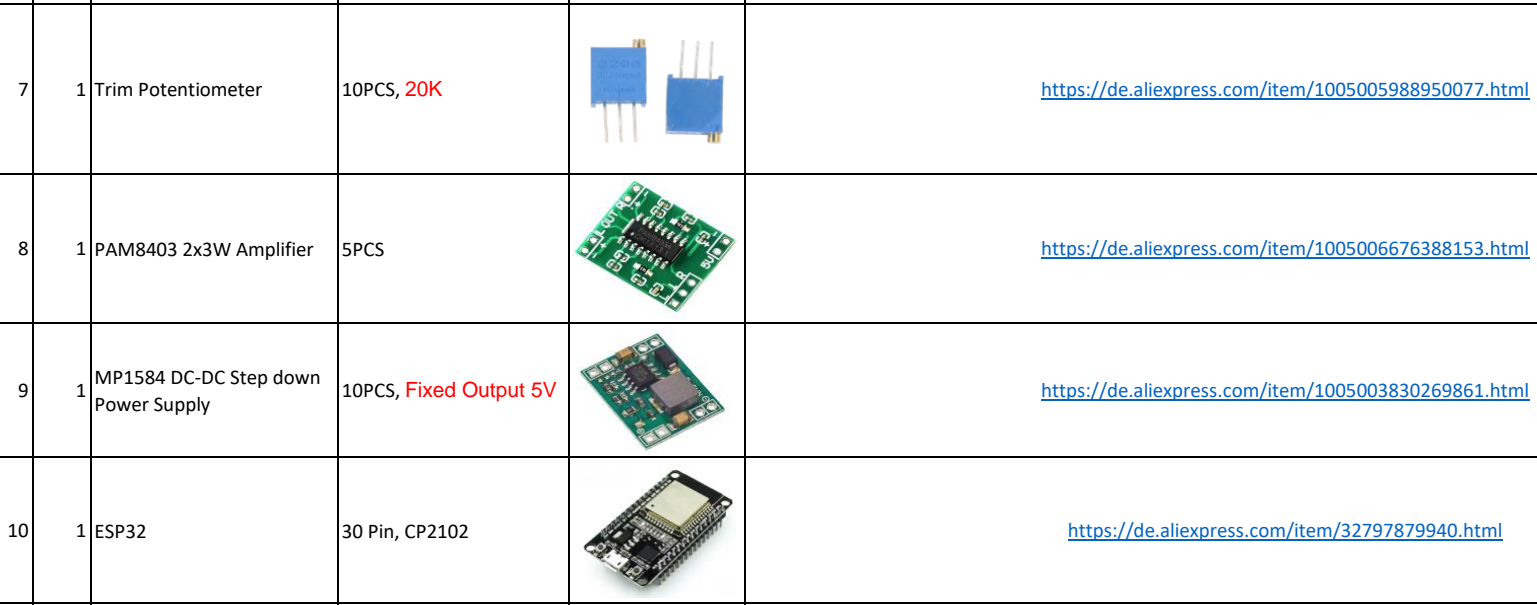
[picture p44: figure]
Trim Potentiometer; 10PCS, 20K; https://de.aliexpress.com/item/1005005988950077.html; PAM8403 2x3W Amplifier; 5PCS; https://de.aliexpress.com/item/1005006676388153.html; ESP32; 30 Pin, CP2102; https://de.aliexpress.com/item/32797879940.html

9 | 1 | MP1584 DC-DC Step down Power Supply | 10PCS, Fixed Output 5V | | https://de.aliexpress.com/item/1005003830269861.html
11 | 1 | 3D printable housing | | | https://thediyguy999.github.io/TheDIYGuy999_ESP32_Web_Flasher/products/ESP32SoundAndLightController/Housing.zip
| | Compiled Software | | | https://thediyguy999.github.io/TheDIYGuy999_ESP32_Web_Flasher/flash.html | Install it, using your browser!

21.9.2024

TheDIYGuy999 | ESP32 Sound and Light Controller SMD V1.2 | Pre assembled PCB and required additional

## components for finalization

Full GitHub Repo | https://github.com/TheDIYGuy999/Rc_Engine_Sound_ESP32 | VS Code recommended

21.9.2024

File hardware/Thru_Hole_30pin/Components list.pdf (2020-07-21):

ESP32 sound and light controller (30 pin version) components list

Software and PCB files: https://github.com/TheDIYGuy999/Rc_Engine_Sound_ESP32
PCB supplier: | https://jlcpcb.com
Schematic pos. | Name | supplier link (affiliate links will support my work by giving me a small provision, but you will not have to pay more)
X1 | 5.08mm Screw Terminal Block | https://www.banggood.com/20pcs-2-Pin-Plug-In-Screw-Terminal-Block-Connector-5_08mm-Pitch-p-993197.html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
IC1 | LM7805 voltage regulator (TO-220) | https://www.banggood.com/10pcs-L7805CV-TO220-L7805-TO-220-7805-LM7805-MC7805-Original-IC-p-1070097.html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
C1 | 25v, 1000uf low ESR capacitor | https://www.banggood.com/150pcs-25V-1000uf-10x16MM-High-Frequency-Low-ESR-Radial-Electrolytic-Capacitor-p-1675367.html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
IC2 | PAM8403 stereo amplifier board | https://www.banggood.com/5pcs-PAM8403-Miniature-Digital-USB-Power-Amplifier-Board-2_5V-5V-p-918227.html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
U1 | ESP32 board (30 pin) | https://www.banggood.com/Geekcreit-ESP32-WiFibluetooth-Development-Board-Ultra-Low-Power-Consumption-Dual-Cores-Unsoldered-p-1214159.html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
JPXX, socket for ESP32 | male & female header 0.1" | https://www.banggood.com/10Pcs-40-Pin-2_54mm-Male-Female-SIL-Socket-Row-Strip-PCB-Connector-p-953436.html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
RXX | 1/4W Resistor (different values) | https://www.banggood.com/1000Pcs-50-Values-14W-Metal-Film-Resistor-Resistance-Assortment-Kit-Set-1-p-1363869.html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
R18 | 20k potentiometer | https://www.banggood.com/10-Value-100pcs-1001M-Trimmer-Resistor-Trim-Pot-Potentiometer-Kit-p-1071345.html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
D1, D2 | 1D5819 Schottky Diode | https://www.banggood.com/50Pcs-1N5819-5819-1A-40V-SCHOTTKY-BARRIER-Diode-p-1006510.html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
QXX (except Q11) | BC337-25 NPN transistor | https://www.banggood.com/200pcs-10-Values-20-Each-TO-92-Transistor-Assortment-Assorted-Kit-BC327-BC337-BC517-BC547-BC548-BC549-BC550-BC556-BC557-BC558-p-1578036.html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
Q11 | IRLZ44N N-Channel Mosfet (TO-220) | https://www.mouser.ch/ProductDetail/Infineon-Technologies/IRLZ44NPBF?qs=9%252BKlkBgLFf15OZZk%252BD0ibg%3D%3D

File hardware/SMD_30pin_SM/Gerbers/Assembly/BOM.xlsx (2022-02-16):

Comment | Designator | QTY | Footprint | LCSC Part #（optional） | Additional Comment
 | ~~JP35~~ | ~~1~~ | ~~1X01~~
 | ~~JP16, JP17, JP18, JP19, JP21, JP22, JP23, JP24, JP25, JP26, JP27, JP28, JP29, JP30, JP31~~ | ~~15~~ | ~~1X02~~
 | ~~JP1, JP2, JP3, JP4, JP5, JP6, JP7, JP8, JP9, JP10, JP11, JP12, JP14,JP34~~ | ~~14~~ | ~~1X03~~
 | ~~JP13~~ | ~~1~~ | ~~1X06~~
 | ~~JP15~~ | ~~1~~ | ~~1X07~~
 | ~~JP20~~ | ~~1~~ | ~~2X03~~
~~WAGO SREW CLAMP~~ | ~~X1~~ | ~~1~~ | ~~W237-132~~
1000uF 10V | C1 | 1 | SMD-ECAP-10x10
2.2uF 25V | C4 | 1 | C1206
10k | R11, R12 | 2 | R0805
200R | R27, R30 | 2 | R0805
~~20k~~ | ~~R18~~ | ~~1~~ | ~~S64W~~ |  | ~~Potentiometer~~
330R | R1, R2, R3, R4, R5, R6, R7, R8, R10 | 9 | R0805
47R | R28 | 1 | R0805
~~DC-DC-STEP-DOWN-MP1584~~ | ~~U$1~~ | ~~1~~ | ~~custom~~
~~ESP32DEVKITV1~~ | ~~U1~~ | ~~1~~ | ~~ESP32-DEVKITV1~~
~~JUMPER-PAD-3-2OF3_NC_BY_TRACE_LARGE~~ | ~~JP32, JP33~~ | ~~2~~
~~OSHW-LOGOM~~ | ~~LOGO1~~ | ~~1~~ | ~~OSHW-LOGO-M~~
~~PAM8403_NO_SPEAKERS~~ | ~~IC4~~ | ~~1~~ | ~~PAM8403_NO_SPEAKERS~~
SS14 | D1, D2 | 2 | SMA-DIODE DO-214AC |  | 40V, 1A Schottky rectifier
SS34 | D3 | 1 | SMA-DIODE DO-214AC |  | 40V, 3A Schottky rectifier
ULN2003AD | IC2, IC3 | 2 | SO16
 | Parts suppliers and tolerances are not important. Please ask back, if any of the SMD components can't be populated
 | Do not populate

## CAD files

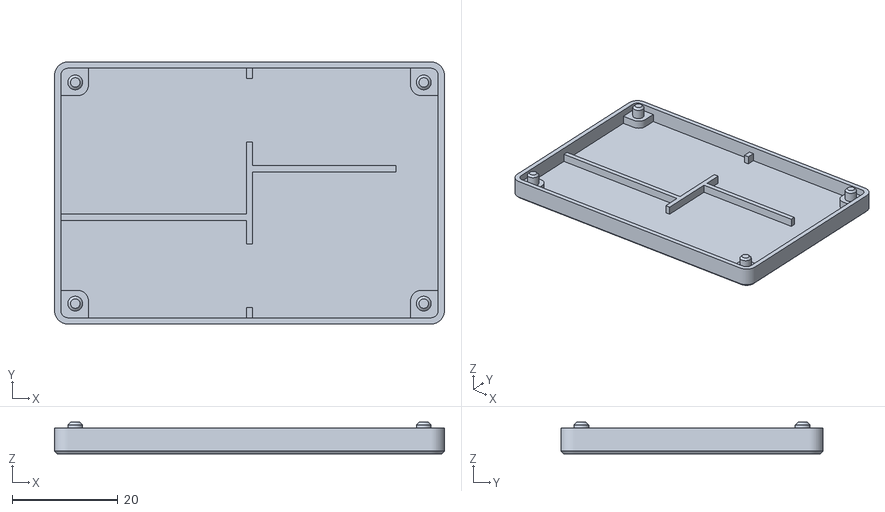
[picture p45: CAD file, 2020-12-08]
hardware/SMDbase.stl
73.9 x 49.7 x 6.00

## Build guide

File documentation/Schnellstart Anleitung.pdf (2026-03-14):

SICHERHEITSVORSCHRIFTEN

TECHNISCHE DATEN | 3
LED-VERKABELUNG | 8

7

10

9

MINIMALE VERDRAHTUNG (SBUS-MODUS)

SYSTEMÜBERSICHT

2

11

PRODUKTBESCHREIBUNG | 4

KANALZUWEISUNG („MICRORC“-AUTOSTYLE-VERSION)

SOFTWAREKONFIGURATION

LINKS

5

# Inhaltsverzeichnis

# ESP32RCSound&LightController

# Kurzanleitung

### Machine Translated by Google

### Sicherheitsbestimmungen

# ESP32RCSound&LightController

# Kurzanleitung

- Dieses Produkt wurde nicht auf FCCorCE-Konformität getestet.

Entwicklung und Anpassung. TheDIYGuy999 übernimmt keinerlei Haftung für Schäden oder Folgeschäden, die aus der Verwendung dieses Systems entstehen.

- Dieses Produkt darf nicht verwendet werden, bis dieses Handbuch vollständig gelesen wurde und
- Dieses Open-Source-Produkt unterliegt der eigenen Verantwortung des Benutzers für die Nutzung, kostenlos
- Dieses Produkt ist nicht für große und gefährliche Modelle geeignet, da es keine
- Trennen Sie immer die Batterie, wenn dieses Produkt nicht verwendet wird. Es zieht immer ein paar Milliampere, auch wenn der ECI ausgeschaltet ist, und entlädt andernfalls die Batterie.
- Isolieren Sie die Fahrzeugverkabelung immer ordnungsgemäß mit Schrumpfschläuchen, um Kurzschlüsse zu vermeiden. Montieren Sie die blanke Leiterplatte niemals direkt auf einer Metallplatte. Dies führt zu Kurzschlüssen.
- Dieses Produkt ist nicht für Kinder unter 14 Jahren geeignet.

Ebenso müssen Sie allen in diesem Kapitel genannten Einschränkungen zustimmen.

- Verwenden Sie dieses Produkt niemals auf öffentlichen Straßen.

Redundanz.

- Schließen Sie niemals Kabel an oder trennen Sie sie, während das Produkt an eine Batterie angeschlossen ist.
- Dieses Produkt ist nicht gegen falsche Polarität geschützt! Überprüfen Sie Ihre Verkabelung immer doppelt, bevor Sie die Batterie anschließen. Eine falsche Polarität zerstört das Produkt sofort.
- Dieses Produkt darf nur an trockenen Orten verwendet werden.

Größe (SMD-Version):
Spannungsbereiche:

13 Kanäle, Anschluss RX

Open Source:

.h-Dateien, 8 Bit, 22050 Hz (variable Abtastrate für die Engine, generiert aus WAV-Dateien mit dem enthaltenen Tool „Audio2Header.html“)

Getriebe:

Viele Fahrzeuge sind bereits konfiguriert: EU-, russische und US-Lastwagen, Panzer, EU- und US-Autos, EU- und US-UV:

comingfromESC

Geräusche:

3,3 VDC (die meisten modernen Receiver arbeiten mit dieser Logikspannung, bei sehr alten Receivern ist jedoch Vorsicht geboten)

Virtuelle Automatik mit Drehmomentwandler, virtuelle Doppelkupplung, Getriebe:

6 Kanäle, Anschlüsse CH1– CH6

1 Ausgang, max. 300 mA

ESC:

Ja (Software und Hardware): https://github.com/TheDIYGuy999/Rc_Engine_Sound_ESP32

Soundkategorien:

Ausgänge:

Arduino „MicroRC“:
FlyskyFS-I6x:

Für die volle Funktionalität ist ein bestimmter Fahrzeugtyp erforderlich.

Der ESC (Crawler-Stil mit Direktbremse) muss an den Ausgang „ESC“ angeschlossen werden. Dies ermöglicht uns die Nutzung der „virtuellen Fahrzeugträgheit“.

6,5 VDC, auch abhängig von den Einschränkungen der anderen Geräte, die an die „+V“-Schiene angeschlossen sind

Definieren Sie Ihr eigenes Profil im Reiter „2_adjustmentsRemote“

Vordefinierte Fahrzeuge: (wählen Sie diese im Reiter „1_adjustmentsVehicle“ aus)

Start, Leerlauf, Hochdrehen, Zündung klopfen, Druckluftbremse, Feststellbremse, Motorbremse, Hupe, Turbo, Abblasventil, Hupe, Sirene, Ton1

Natürlich können Sie auch Ihre eigenen Fahrzeugkonfigurationen erstellen

Allgemein:

Batterieversorgungsspannung: Der Eingangsversorgungsspannungsbereich beträgt 7–12,6 VDC (2S oder 3S LiPo). Maximale „Sig“-
Spannung:

74 x 50 x 25 mm (einschließlich Anschlüsse und Bodenschale)

Schaltgetriebe: TAMIYA 3-Gang, virtueller 3-Gang (geschaltet durch 3-Positionen-Schalter)

8 Kanäle, Anschluss RX

Automatisch

13 Kanäle, Anschluss RX

5VDC Motorvibrationssimulation Shaker Ausgang:

Ausgangsspannung:
Eingangssignaltypen:

Sonstiges:

Es können 1 oder 2 Lautsprecher mit 4–8 Ohm angeschlossen werden

jeweils mit 3,4 oder 6 Gängen

Kompatible Fernbedienungen: (vordefinierte Profile im Reiter „2_adjustmentsRemote“)

Traktoren, Motorräder, Flugzeuge, Lokomotiven …

PWM:
PPM:
SBUS:
IBUS:

Lautsprecherausgänge:
5VDC-Ausgänge für LED: 11 Kanäle, alle mit PWM-Helligkeitsregelung, gemeinsamer Pluspol, immer einen Serienwiderstand verwenden, max. 100mA pro Kanal

SBUS-Modus empfohlen, Dual-Rate-Switching erforderlich 100 %/75 %

5VDC für LED, Shaker und Verstärker, max. 1A gesamt

Sounddateityp:

Maximale „+V“-Spannung

# Kurzanleitung

# ESP32RCSound&LightController

# Technische Daten

# Kurzanleitung

# ESP32RCSound&LightController

Erforderliches USB-Kabel:

Kanalumkehr

Selbstverständlich lässt sich damit auch die komplette Fahrzeug- und Anhängerbeleuchtung steuern. Alle LEDs lassen sich mittels PWM (Pulsweitenmodulation) in der Helligkeit variieren. So lassen sich die hohe Stromaufnahme beim Anlassen des Motors, sanftes Schalten von Glühlampenblinkern , Fern- und Abblendlicht, Xenon -Zündlicht etc. simulieren.

Das Modul ist mit den meisten Remote-Systemen kompatibel , die PWM, PPM, SBUS oder IBUS verwenden .

Dieser Open-Source-RC-Sound- und Lichtcontroller ist hauptsächlich für RC-Trucks im Maßstab 1:14 wie den TAMIYA King Hauler gedacht. Natürlich kann er auch für alle Arten anderer Fahrzeuge verwendet werden, sofern er hineinpasst. Er ist ein guter Ersatz für den TAMIYA AMFC-01 oder MFC-03 und bietet deutlich mehr Realismus.

Damit lassen sich Fahrzeuggeräusche wie Motorgeräusche, Hupen, Sirenen, Bremsgeräusche etc. steuern. Es können mehrere Sounds gleichzeitig abgespielt werden. Der Motorsound wird spontan aus mehreren Sounds wie Leerlauf, Drehzahl, Turbo, Dieselgeräusch etc. zusammengemischt . Die Lautstärke des Motorsounds ist last- und drehzahlabhängig . Dadurch klingt der Motor sehr realistisch.

Ja, wenn aktiviert im Reiter „2_adjustmentsRemote“

Automatische Nullkalibrierung des Eingangskanals:

Hochladen und Konfigurieren:

Konfiguration:

ATAMIYA Anhängerlichtsatz 56502 im Lagerzustand, anschließbar.

Kommunikation. Ein flexibles Kanalmapping ist implementiert. Details finden Sie in der mitgelieferten Datei „adjustmentsRemote.xlsx“.

Flexibles
Kanalmapping:

MicroUSB

Ja, gemäß den Einstellungen im Reiter „2_adjustmentsRemote“

Viele Fahrzeuge sind bereits vorkonfiguriert und können einfach ausgewählt werden. Natürlich können Sie auch eigene Konfigurationen vornehmen, ohne den Arduino-Hauptcode zu ändern.

Ja, nach dem Einschalten, sofern im Reiter „2_adjustmentsRemote“ aktiviert

Es bietet außerdem einzigartige Funktionen wie virtuelle Fahrzeugträgheit, synchronisiertes TAMIYA-3-Gang-Getriebe (in der Software), virtuelle manuelle und automatische Getriebe. All diese Funktionen sorgen für ein sehr flüssiges und realistisches Fahrverhalten des Fahrzeugs.

Ein Shaker-Ausgang ist ebenfalls enthalten. Er wird verwendet, um den Shaker-Motor mit einem exzentrischen Gewicht anzutreiben und so Motorvibrationen zu simulieren.

Anpassungen erfolgen in ArduinoIDE, min. Version 1.7.4

## Produktbeschreibung

RX-Eingang (SBUS,

LED-Ausgangskanäle

LED

ESP32-
Mikrocontroller

Lautstärkepotentiometer

Batterieanschluss

2xLautsprecher

TrailerLED

ESC-Ausgabe

Anschluss

Micro-USB-Programmieranschluss

Anschluss | Universalausgang

Shaker
Anschlüsse

Tamiya
6PWM-Eingangskanäle

IBUS,PPM)

Rücklicht

Anschluss

# Systemübersicht

# ESP32RCSound&LightController

# Kurzanleitung

# Kurzanleitung

# ESP32RCSound&LightController

LED-Treiber

Es werden nur die SMD-Bauteile bestückt, die restlichen bedrahteten Bauteile müssen Sie selbst verlöten. Siehe Anleitungsvideo: https://www.youtube.com/watch?v=csQgTfxRd8Y&t=1s

https://github.com/TheDIYGuy999/Rc_Engine_Sound_ESP32/tree/master/Eagle_PCB/SM

Diese Ansicht zeigt eine unfertige Platine, wie sie von PCBWay.com geliefert wird. So bestellen Sie sie:

D

Außerdem wird die Steckeranordnung im Detail dargestellt. CH1–4 sind Steckerpaare, wodurch keine Kabel mehr erforderlich sind.

5V-Regler

ULN2003

PAM8403Verstärker geht hierhin

Beachten Sie, dass die LED mit einem gemeinsamen Pluspol verdrahtet werden muss. Das bedeutet, dass die langen LED-Beine (die +-Seite) mit einem gemeinsamen 5-V -Potenzial verbunden werden können. Die negative Seite jeder LED (das kurze Kabel) muss mit einem geeigneten Strombegrenzungswiderstand und dann mit dem LED-Ausgangspin verbunden werden.

Wird ein Anhängerlichtset „TAMIYA 56502“ an den entsprechenden Stecker angeschlossen, sind keine zusätzlichen Strombegrenzungswiderstände erforderlich. Diese sind bereits auf der Platine enthalten.

Weitere Einzelheiten finden Sie im Kapitel „LED-Verkabelung“.

SBUSout(TX)

SBUSin(RX)

DuPont-

Kabelanschluss
GND,
+Wassersignal

Es wird dringend empfohlen, zwischen der Batterie und der restlichen Verkabelung eine Sicherung hinzuzufügen !

„MicroRC“-
Empfänger

Überprüfen Sie die gesamte Verkabelung

4-8Ohm-Lautsprecher

Versorgungsadapter (parallel zum ESC-Stromanschluss
verdrahtet)

Stromanschluss

2SLiPo

Anschluss

3-adrig

Achten Sie vor dem Anschließen der Batterie auf die richtige Polarität! Eine falsche Polarität führt zur sofortigen Zerstörung des Controllers.

ESC

Überbrückungskabel von „+V“ auf „5V“ (entfernen, wenn
ein ESC verwendet wird)

HINWEIS: In diesem Beispiel ist kein ESC an den ESC-Anschluss und den ESC-Stromanschluss angeschlossen. Daher müssen wir den ESP32 und den Empfänger (+V-Schiene) über das abgebildete Jumper-Kabel mit 5V vom internen 5V-Regler versorgen. Dieses Jumper-Kabel muss entfernt werden, wenn ein ESC angeschlossen ist. In diesem
Fall wird der ESP32 über die Batterie-Entladeschaltung (BEC) versorgt, die heutzutage in den meisten ESCs integriert ist. Der Akku muss nicht abgeklemmt werden, wenn Sie das USB-Kabel anschließen, da dort eine Anti-Rückspeisediode (D1) vorhanden ist.

ESC

R

## Minimale Verkabelung (SBUS-Modus)

# ESP32RCSound&LightController

# Kurzanleitung

eigenen Serienwiderstand.

- Beachten Sie auch, dass der maximale Summenstrom für die gesamte 5-V-Schiene, die geliefert wird

220

Flache Stelle

die integrierten ULN2003-LED-Treiber.
- Wenn mehr als eine LED parallel zu einem LED-Ausgangspin verdrahtet ist, benötigt jede

orange
grün
weiß
blau

5V-Stift

Ausgangspins (außer dem TAMIYA-Anhängerstecker). Dies wird dauerhaft beschädigt

rot 1,8 1,9 2 3

Wie bereits erwähnt beträgt die LED-Versorgungsspannung 5 V und kommt vom internen Regler.

150

150

Langbein

- Der maximale durchschnittliche LED-Ausgangsstrom pro Kanal beträgt 100 mA. Es wird jedoch nicht empfohlen, jeden Kanal mit diesem Strom zu belasten. Andernfalls kann der ULN2003-LED-Treiber überhitzen. Überprüfen Sie ihn nach dem Verkabeln eines neuen Fahrzeugs mindestens 10 Minuten lang auf übermäßige Temperaturanstiege. Wenn die Temperatur zu hoch ist, sollten Sie einen externen Treibertransistor für die LED verwenden.

https://www.digikey.de/en/resources/conversion-calculators/conversion-calculator-led-series-resistor

Ein üblicher maximaler LED-Strom beträgt 15 mA.

- Zwei rote oder orangefarbene LEDs können in Reihe geschaltet werden. Dies macht die Schaltung effizienter.

Die folgende Tabelle enthält die erforderlichen Mindestwerte für den Serienwiderstand:

- Schließen Sie niemals LEDs oder andere Geräte ohne einen geeigneten Vorwiderstand an die LED an.

Sie können auch einen Taschenrechner verwenden, um den richtigen Wert zu ermitteln:

- Bei falschem Anschluss leuchtet die LED nicht .

200

In diesem Fall müssen Sie für die Berechnung des Serienwiderstands beide Serienspannungen addieren.

durch den Bordregler beträgt 1A.

220

LED-Farbe Durchlassspannung [Volt] Mindestwiderstand [Ohm]

3

Vorwiderstand

# Kurzanleitung

# ESP32RCSound&LightController

LED-Verkabelung

# Kurzanleitung

# ESP32RCSound&LightController

# Kanalzuweisung (Version im Autostil „Micro RC“)

Modus 1:

CH8: Motor
an/aus

Getriebeneutral

Modus 2:

Zustand+ | Motorbremse/

CH4:3 Tasten

CH5: Hupe,
Sirene, Blaulicht

CH1: Lenkung
und Blinker

Ton1

CH3: Gas und
Bremse
Lichthupe, | Lichter
Fern-/
Abblendlicht

Volumen

CH2:Getriebegänge
1-3

# Softwarekonfiguration

# ESP32RCSound&LightController

# Kurzanleitung

Nehmen Sie die Anpassungen auf der Registerkarte „Anpassungen“ vor. Ändern Sie den Code auf der Registerkarte „Main“ nicht.

Fernbedienung

Installieren Sie

diese Bibliotheken

Die
Anpassungsregisterkarten oben
Übertragung | Shaker

Einzelheiten finden Sie unter:

https://github.com/TheDIYGuy999/Rc_Engine_Sound_ESP32/blob/master/README.md

Fahrzeug
Registerkarte „Wartung“

Softwareversion

Erforderliche
Boardeinstellungen

Installationsboarddefinition

ESC

# Kurzanleitung

# ESP32RCSound&LightController

Entworfen in der Schweiz von TheDIYGuy999

Videos:
https://www.youtube.com/channel/UCqWO3PNCSjHmYiACDMLr23w

Links
Software- und Hardware-Downloads: https://github.com/TheDIYGuy999/Rc_Engine_Sound_ESP32

Readme:
https://github.com/TheDIYGuy999/Rc_Engine_Sound_ESP32/blob/master/README.md

Forum:
https://www.rc-modellbau-portal.de/index.php?threads/esp32-arduino-rc-sound-und-licht-controller.7183/

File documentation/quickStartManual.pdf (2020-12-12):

# ESP32 RC Sound & Light Controller

## Quick Start Manual

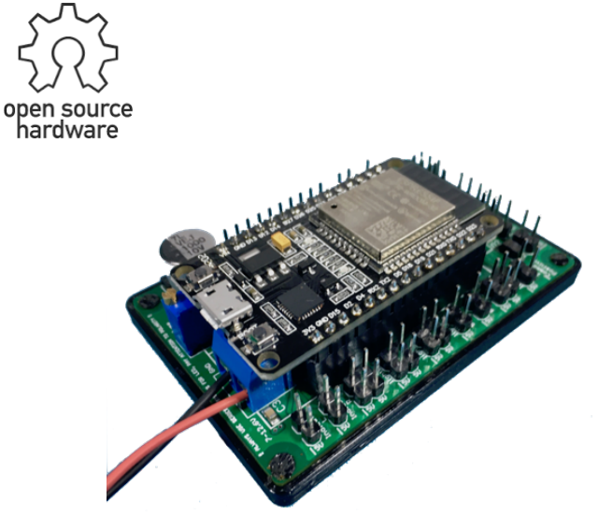
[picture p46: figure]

## Table of Contents

SAFETY REGULATIONS | 2
TECHNICAL SPECIFICATIONS | 3
PRODUCT DESCRIPTION | 4
SYSTEM OVERVIEW | 5
MINIMUM WIRING (SBUS MODE) | 7
LED WIRING | 8
CHANNEL ASSIGNMENT (“MICRO RC” CAR STYLE VERSION) | 9
SOFTWARE CONFIGURATION | 10
LINKS | 11

# ESP32 RC Sound & Light Controller

## Quick Start Manual

## Safety regulations

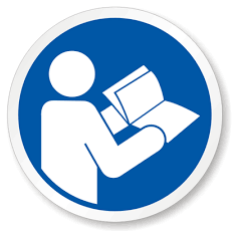
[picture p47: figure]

- This product must not be used until this manual has been fully read and understood. Likewise, you must agree with all the restrictions mentioned in this chapter.
- This open source product is left to the user's own responsibility for use, free development and customization. TheDIYGuy999 assumes no liability whatsoever for any damage or consequential damage resulting from the use of this system.
- This product is not suitable for large and dangerous models, because there is no redundancy.
- Never use this product on public roads.
- This product has not been tested for FCC or CE compliance.
- Never connect or disconnect wires while the product is connected to a battery.
- Always disconnect the battery, if this product is not in use. It always draws a couple of Milliamps, even if the ESC is switched off and will drain the battery otherwise.
- This product is not protected against wrong polarity! Always double check your wiring before connecting the battery. Wrong polarity will immediately destroy the product.
- Always insulate the vehicle wiring properly, using heat shrinks in order to prevent short circuits. Never mount the bare PCB directly on top of a metal plate. This will cause short circuits.
- This product may only be used in dry locations.
- This product is not suitable for children below 14 years.

# ESP32 RC Sound & Light Controller

## Quick Start Manual

## Technical specifications

General:
Open Source: | Yes (Software & Hardware):
| https://github.com/TheDIYGuy999/Rc_Engine_Sound_ESP32
Size (SMD version): | 74x50x25mm (including connectors and bottom shell)
Voltage ranges:
Battery supply voltage: The input supply voltage range is 7 – 12.6VDC (2S or 3S LiPo)
Maximum “Sig” voltage: | 3.3VDC (most modern receivers are working with this logic
| voltage, but you have to be careful with very old receivers)
Maximum “+V” voltage coming from ESC | 6.5VDC, also depending on the limitations of the other devices, which are connected to the “+V” rail
Output voltage: | 5VDC for LED, shaker and amplifier, max. 1A in total
Input signal types:
PWM: | 6 channels, connectors CH1 – CH6
PPM: | 8 channels, connector RX
SBUS: | 13 channels, connector RX
IBUS: | 13 channels, connector RX
Outputs:
Speaker outputs: | 1 or 2 speakers with 4 – 8 Ohms can be connected
5VDC outputs for LED: 11 channels, all with PWM brightness control, common positive,
| always use a series resistor, max. 100mA per channel
5VDC engine vibration simulation shaker out: | 1 output, max. 300mA
ESC: | The ESC (crawler style with direct brake) needs to be connected to
| the “ESC” output. This allows to use the “virtual vehicle inertia”
Compatible remotes: (predefined profiles in the “2_adjustmentsRemote” tab)
Arduino “Micro RC”: | Car style type required for full functionality
Flysky FS-I6x: | SBUS mode recommended, dual rate switching required 100% /
| 75%
Others: | Define your own profile in the “2_adjustmentsRemote” tab
Sounds:
Sound file type: | .h files, 8bit, 22050Hz (variable sampling rate for engine, generated out of wav files using the included tool
| “Audio2Header.html”)
Sound categories: | Start, idle, revving, ignition knock, air brake, parking brake, engine brake, horn, turbo, blow-off valve, horn, siren, sound 1

Transmissions:
Manual transmissions: TAMIYA 3 speed, virtual 3 speed (shifted by 3 pos. switch)
Automatic transmissions: | Virtual automatic with torque converter, virtual double clutch,
| each with 3, 4 or 6 gears
Predefined vehicles: | (select them in the “1_adjustmentsVehicle” tab)
A lot of vehicles are already configured: | EU, Russian & US trucks, tanks, EU & US cars, EU & US SUV,
| tractors, motorcycles, planes, locomotives…
| Of course, you can also make your own vehicle configurations

# ESP32 RC Sound & Light Controller

## Quick Start Manual

Configuration:
Required USB lead: | Micro USB
Upload and config: | Adjustments are done in Arduino IDE, min. version 1.7.4
Input channel auto zero calibration: | Yes, after power-on, if enabled in “2_adjustmentsRemote” tab
Channel reversing | Yes, if enabled in “2_adjustmentsRemote” tab
Flexible channel mapping: | Yes, according to settings in “2_adjustmentsRemote” tab

## Product description

This open source RC sound and light controller is mainly intended for 1/14 scale RC trucks like the TAMIYA King Hauler. Of course, it can also be used for all kinds of other vehicles, as long as it fits inside. It is a good replacement for the TAMIYA MFC-01 or MFC-03 and offers way more realism.

A lot of vehicles are pre-configured and can easily be selected. Of course, you can also make your own configurations without changing the Arduino main code.

It can be used to control the vehicle sounds like engine sounds, horns, sirens, brake sounds etc. Multiple sounds can be played at the same time. The engine sound is mixed together on the fly, using multiple sounds like idle, revving, turbo, Diesel knock etc. The engine sound volume is load- and RPM-dependent. This makes the engine sound very realistic.

It also offers unique features like virtual vehicle inertia, synchronized TAMIYA 3 speed transmission (in software), virtual manual and automatic transmissions. All these features make the vehicle drive behavior very smooth and realistic.

Of course, it also is able to control the entire vehicle and trailer lighting. All the LED can be varied in brightness, using PWM (Pulse Width Modulation). This allows to simulate the huge current draw while cranking the engine, smooth switching incandescent bulb indicators, high & low beam, Xenon ignition flash etc.

A TAMIYA trailer light set 56502 in stock condition can be connected.

A shaker output is included as well. It is used to drive a shaker motor with an eccentric weight to simulate engine vibrations.

The module is compatible with most remote systems, which use PWM, PPM, SBUS or IBUS communication. A flexible channel mapping is implemented. For details refer to the included “adjustmentsRemote.xlsx”

# ESP32 RC Sound & Light Controller

## Quick Start Manual

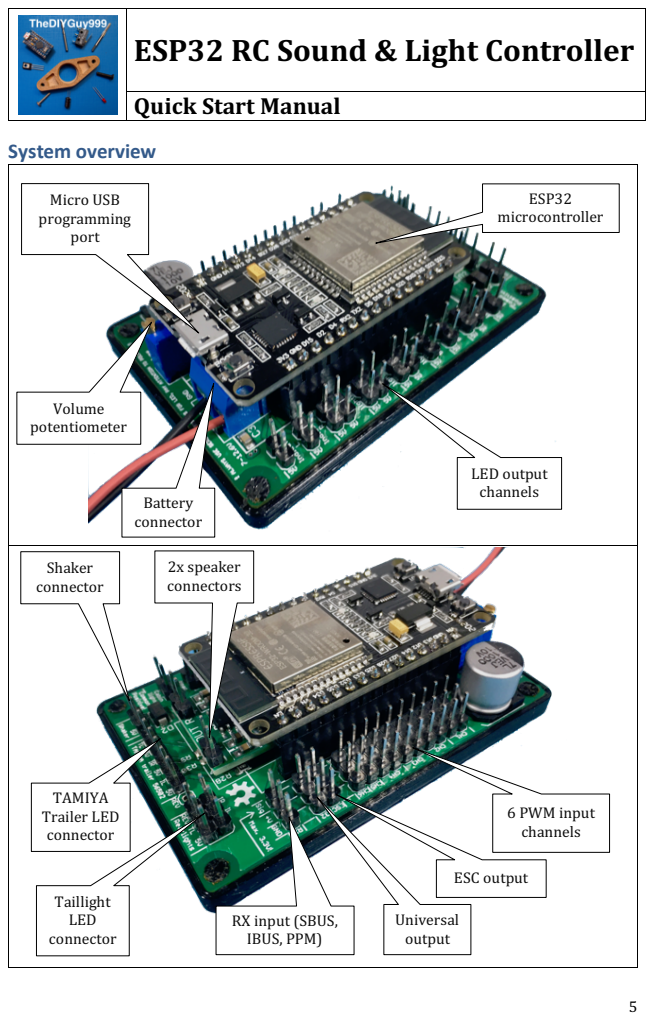
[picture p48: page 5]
System overview; Volume potentiometer; LED output channels; Micro USB programming port; Battery connector; 6 PWM input channels; Shaker connector; ESP32 microcontroller; Taillight LED connector; TAMIYA Trailer LED connector; ESC output; Universal output; 2x speaker connectors

RX input (SBUS,
IBUS, PPM)

# ESP32 RC Sound & Light Controller

## Quick Start Manual

This view shows an unfinished board as it is delivered by PCBWay.com. How to order it: https://github.com/TheDIYGuy999/Rc_Engine_Sound_ESP32/tree/master/Eagle_PCB/SM D

Only the SMD components are populated, the remaining through hole components need to be soldered by yourself. See instructions video: https://www.youtube.com/watch?v=csQgTfxRd8Y&t=1s

It also shows the connector layout in detail. CH1 – 4 are connector pairs, which eliminate the need for y-cables.

Note, that the LED need to be wired “common positive”. This means, that the long LED legs (the + side) can be wired together, using a shared 5V potential. The negative side of each LED (the short wire) needs to be wired to an appropriate current limiting resistor and then to the LED output pin.

If a "TAMIYA 56502 trailer light set is connected to the corresponding connector, no additional current limiting resistors are required. They are already included on the PCB.

For more details, refer to the chapter “LED wiring”

ULN2003
LED driver

5V
regulator

PAM8403
amplifier
goes here

# ESP32 RC Sound & Light Controller

## Quick Start Manual

## Minimum wiring (SBUS mode)

NOTE: in this example, no ESC is connected to the “ESC” connector and to the ESC power connector. So, we have to supply the ESP32 and the receiver (+V rail) with 5V from the internal 5V regulator, via the shown jumper wire. This jumper wire needs to be removed, if an ESC is connected. In this case, the ESP32 is supplied by the battery eliminator circuit (BEC), which is integrated in most ESC these days. You don’t need to disconnect the battery, if you connect the USB cable, there is an anti backfeed diode (D1).

Supply adapter (wired in
parallel with the ESC
power connector)

ESC
power

Jumper wire from “+V”
to “5V” (remove it, if
an ESC is used)

ESC
connector

SBUS
out (TX)

SBUS
in (RX)

2S LiPo

3 wire
DuPont
cable
connecting
GND, +V
and signal

Double check the entire wiring for correct polarity before you connect the battery! Wrong polarity will immediately
destroy the controller.

It is strongly recommended to add a fuse between the battery and the rest of the wiring!

“Micro RC”
receiver

4 - 8 Ohms
speaker

# ESP32 RC Sound & Light Controller

## Quick Start Manual

## LED wiring

As already mentioned, the LED supply voltage is 5V, coming from the internal regulator. A common LED maximum current is 15mA.

The following chart provides the required minimum series resistor values:
LED color | Forward voltage [Volts] | Minimum resistor [Ohms]
red | 1.8 | 220
orange | 1.9 | 220
green | 2 | 200
white | 3 | 150
blue | 3 | 150
You can also use a calculator in order to determine the correct value: https://www.digikey.de/en/resources/conversion-calculators/conversion-calculator-led-series-resistor
- The LED will not light up, if connected the wrong way around.
- Never connect LED or other devices without a suitable series resistor to the LED output pins (except the TAMIYA trailer connector). This will permanently damage the integrated ULN2003 LED drivers.
- If more than one LED is wired in parallel to an LED output pin, each one needs its own series resistor.
- Two red or orange LED can be wired in series. This makes the circuit more efficient. In this case you need to add both series voltages together for the series resistor calculation.
- The maximum average LED output current per channel is 100mA. However, it is not recommended to load each channel with this current. Otherwise, the ULN2003 LED driver may overheat. Always check it for excessive temperature raise for at least 10 minutes after you wired a new vehicle. If the temperature is too high to the touch, you should use an external driver transistor for the LED.
- Also note, that the maximum sum current for the entire 5V rail, which is supplied by the on-board regulator is 1A.

5V pin Long leg

Series resistor

Flat spot

# ESP32 RC Sound & Light Controller

## Quick Start Manual

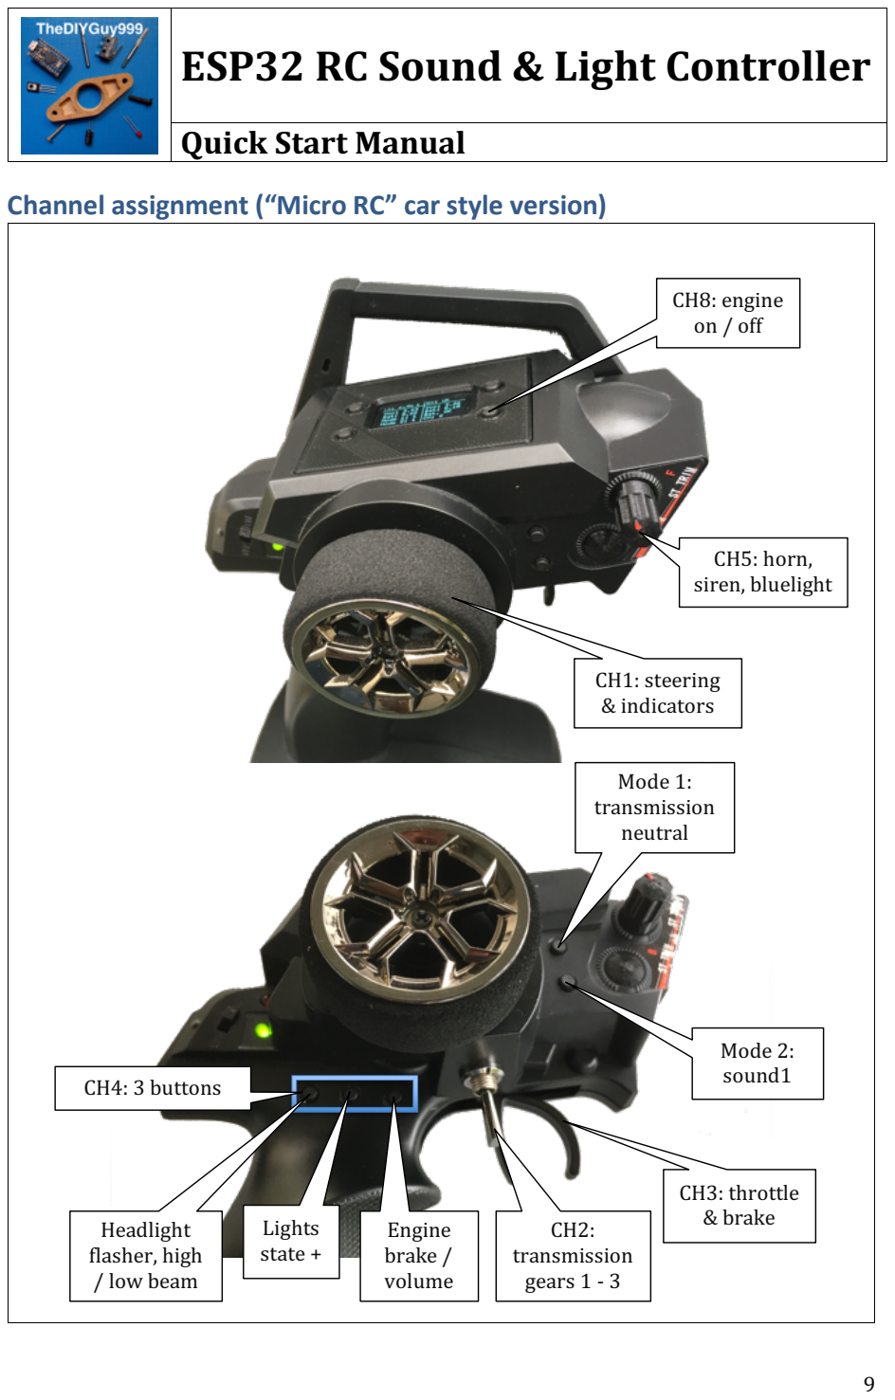
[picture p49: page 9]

## Channel assignment (“Micro RC” car style version)

CH1: steering
& indicators

CH5: horn,
siren, bluelight

CH3: throttle
& brake

Mode 1:
transmission
neutral

CH2:
transmission
gears 1 - 3

Mode 2:
sound1

CH8: engine
on / off

Lights
state +

Engine
brake /
volume

Headlight
flasher, high
/ low beam

CH4: 3 buttons

# ESP32 RC Sound & Light Controller

## Quick Start Manual

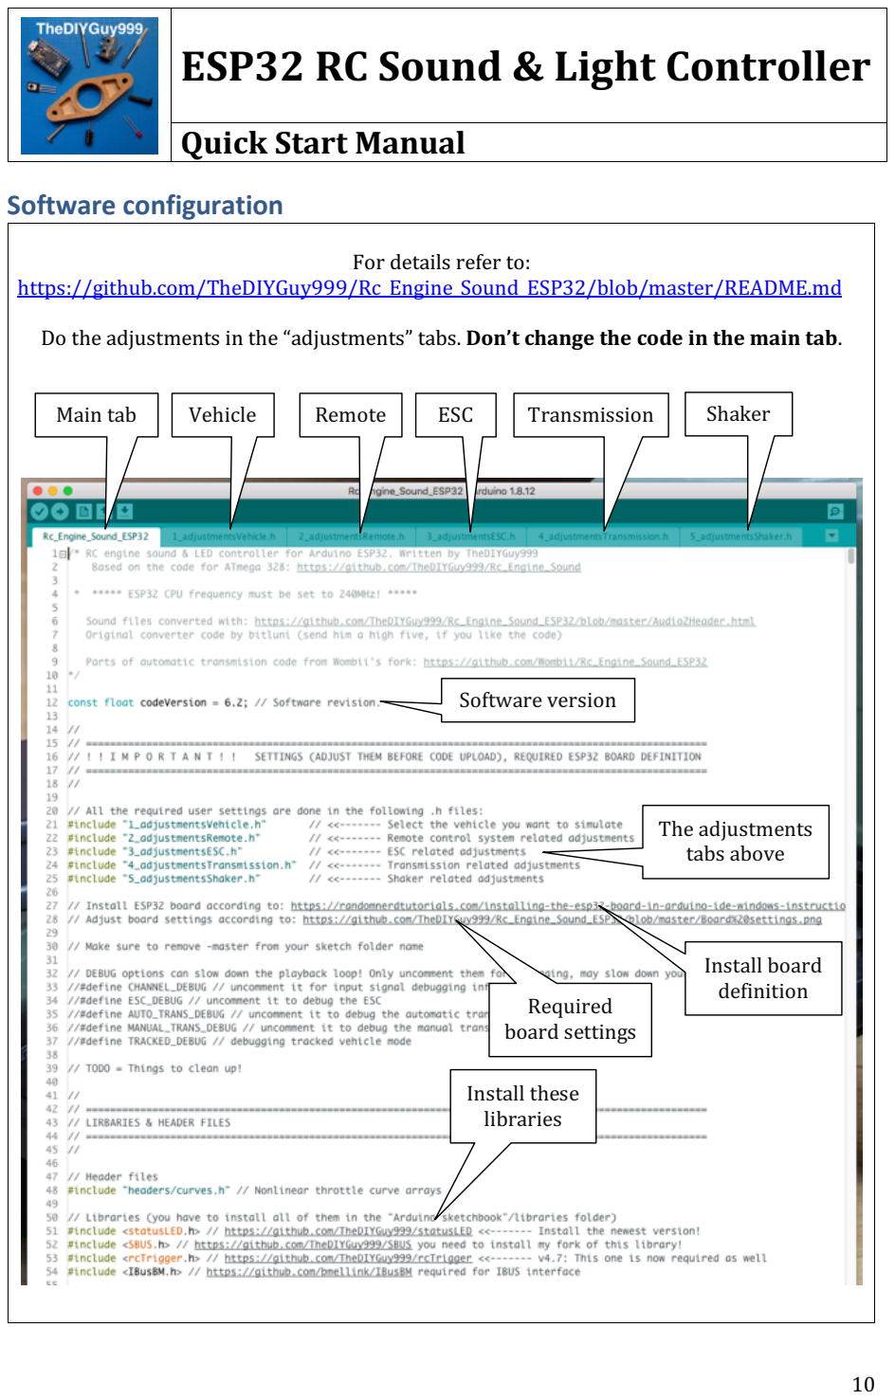
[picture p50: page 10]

## Software configuration

For details refer to:
https://github.com/TheDIYGuy999/Rc_Engine_Sound_ESP32/blob/master/README.md

Do the adjustments in the “adjustments” tabs. Don’t change the code in the main tab.

Install these
libraries

Vehicle

The adjustments
tabs above
Remote | ESC | Transmission | Shaker

Install board
definition
Required
board settings

Software version

Main tab

# ESP32 RC Sound & Light Controller

## Quick Start Manual

## Links

Software and hardware downloads: https://github.com/TheDIYGuy999/Rc_Engine_Sound_ESP32
Readme:
https://github.com/TheDIYGuy999/Rc_Engine_Sound_ESP32/blob/master/README.md Videos:
https://www.youtube.com/channel/UCqWO3PNCSjHmYiACDMLr23w
Forum:
https://www.rc-modellbau-portal.de/index.php?threads/esp32-arduino-rc-sound-und-licht-controller.7183/

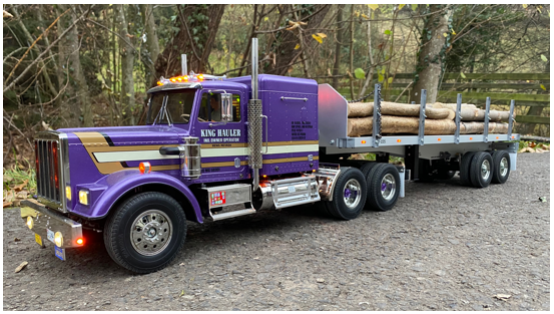
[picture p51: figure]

Designed in Switzerland by TheDIYGuy999

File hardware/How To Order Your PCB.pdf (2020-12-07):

# How To Order Assembled PCB’s on PCBWay

PCBWay offers high quality prototype PCB manufacturing and assembling services with short turnaround times for cheap.

1. Go to: https://github.com/TheDIYGuy999/Rc_Engine_Sound_ESP32
2. Hit “Code” > “Download ZIP”

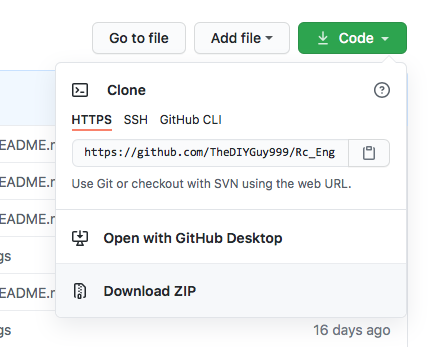
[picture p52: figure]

3. Go to: https://www.pcbway.com/orderonline.aspx
4. Hit
5. Hit
6. Open the ZIP you downloaded before, navigate to the “Gerbers.zip” and select it

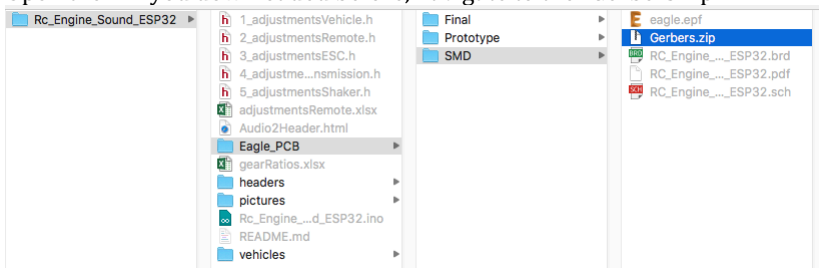
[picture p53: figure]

# How To Order Assembled PCB’s on PCBWay

7. The following preview window opens. If the preview looks OK, select the quantity and the surface finish in the preview screen below (I recommend “HASL lead free”). Maybe you also want to change the solder mask color. Do not change other settings.

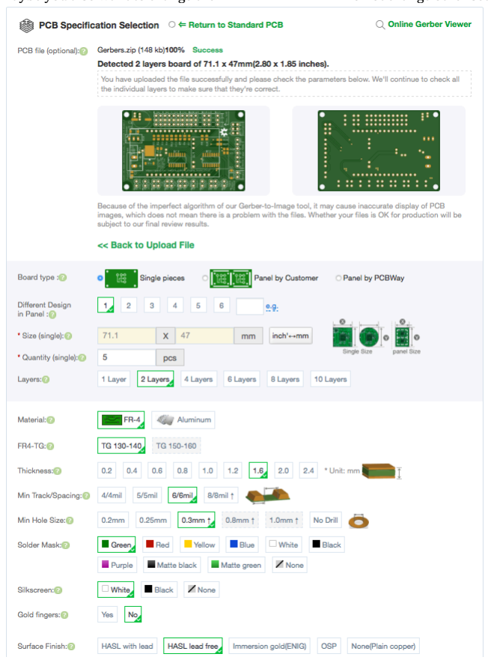
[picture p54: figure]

# How To Order Assembled PCB’s on PCBWay

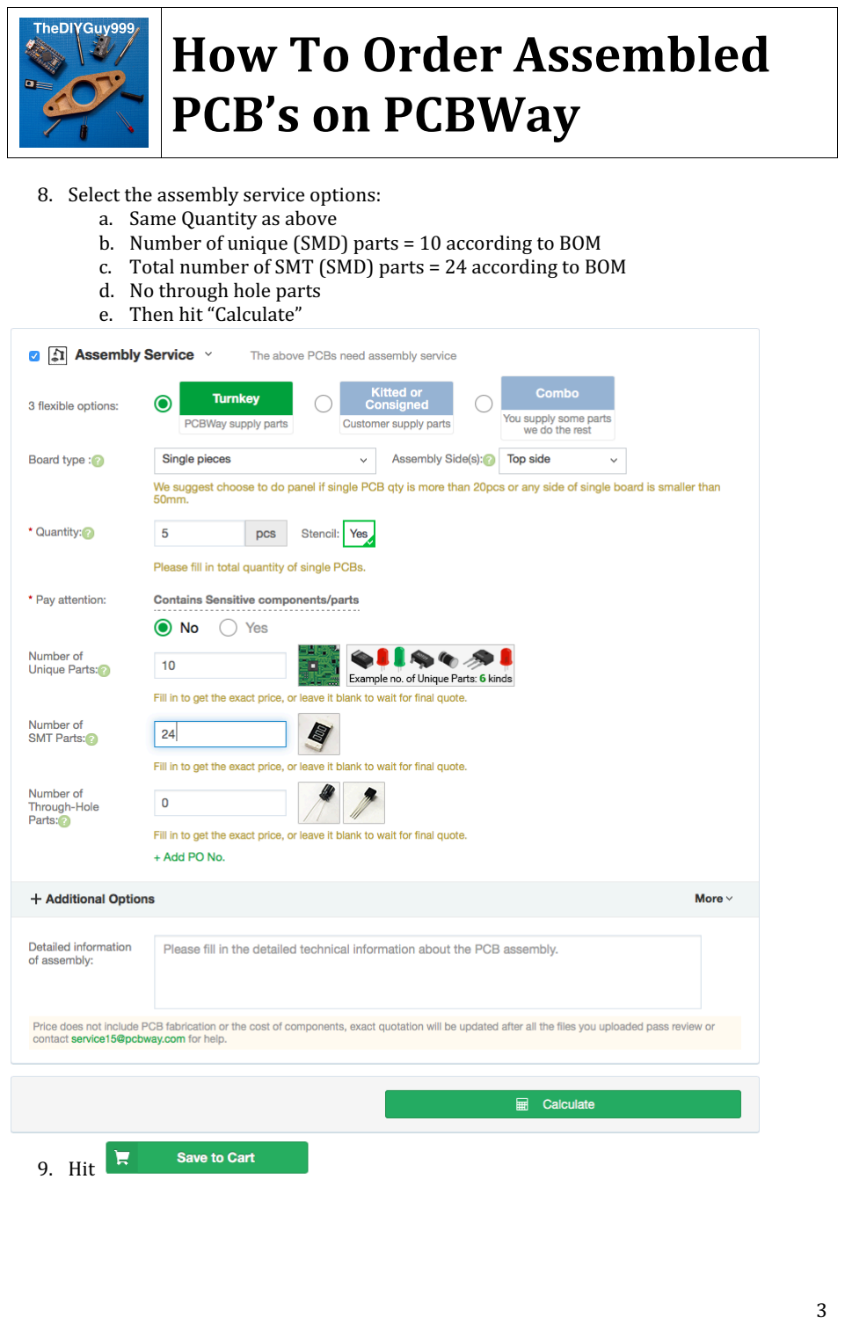
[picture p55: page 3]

8. Select the assembly service options:
a. Same Quantity as above
b. Number of unique (SMD) parts = 10 according to BOM
c. Total number of SMT (SMD) parts = 24 according to BOM
d. No through hole parts
e. Then hit “Calculate”
9. Hit

# How To Order Assembled PCB’s on PCBWay

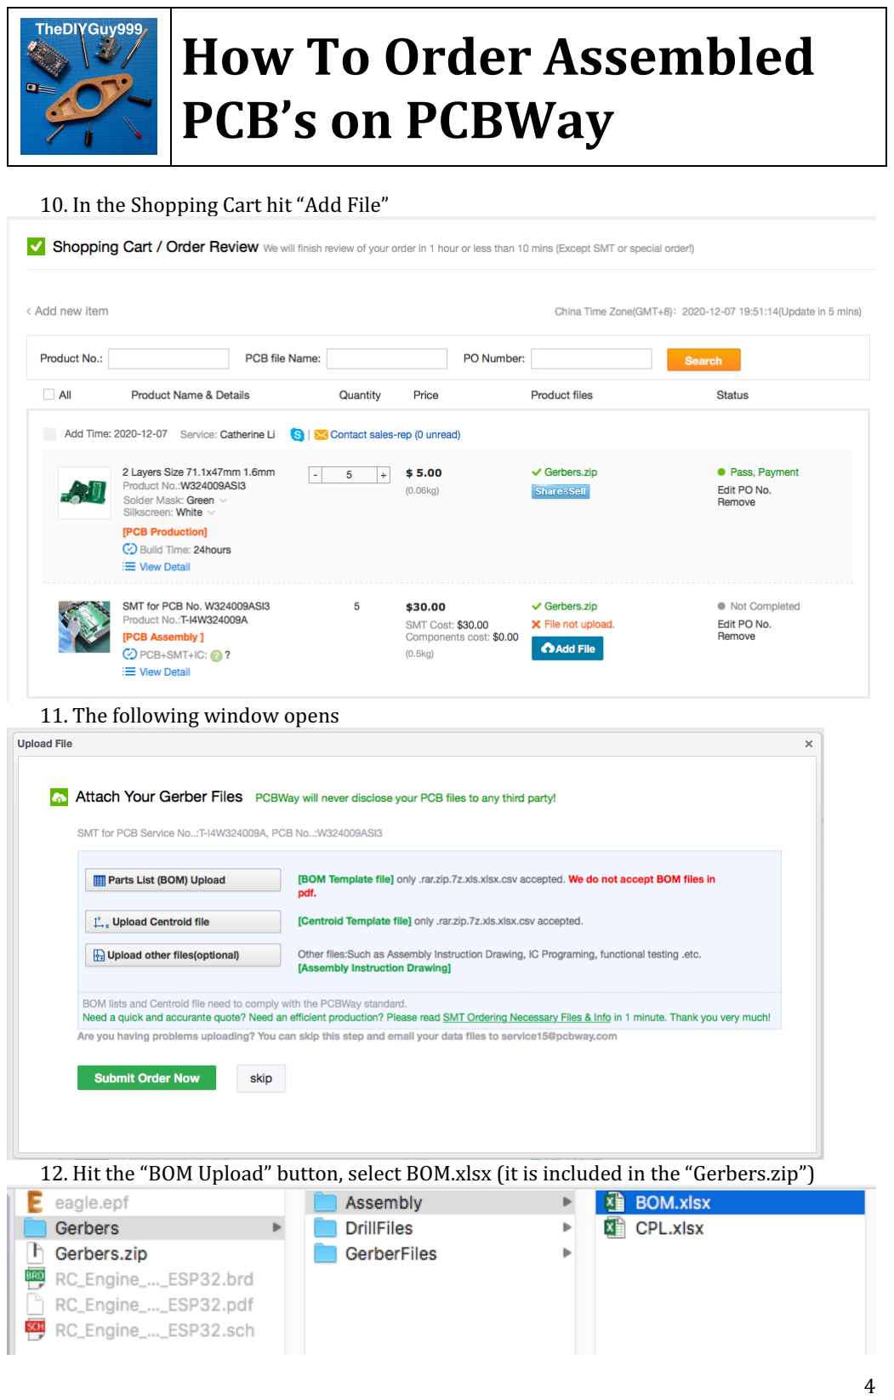
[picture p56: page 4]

10. In the Shopping Cart hit “Add File”
11. The following window opens
12. Hit the “BOM Upload” button, select BOM.xlsx (it is included in the “Gerbers.zip”)

# How To Order Assembled PCB’s on PCBWay

13. Hit the “Centroid File” button, select CPL.xlsx (it is included in the “Gerbers.zip”)
14. Both files are now listed in the window and you are ready to hit “Submit Order Now”

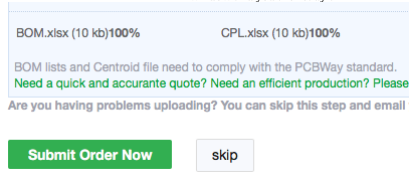
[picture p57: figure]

15. That’s it! PCBWay will contact you soon and send you a final offer
16. After the first board is assembled, PCBWay will send you a picture for confirmation

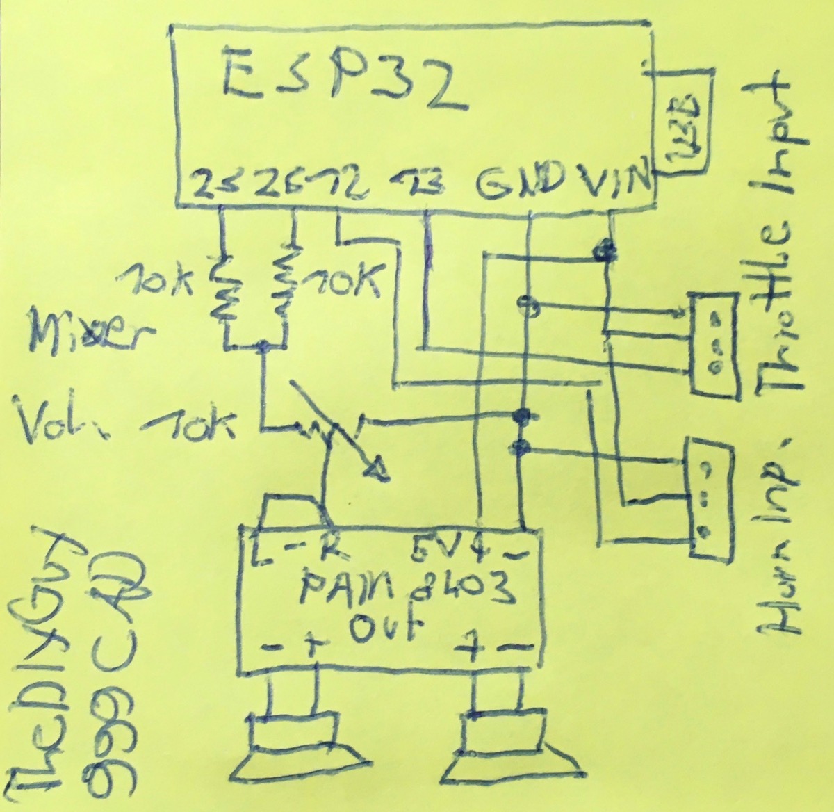
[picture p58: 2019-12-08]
documentation/pictures/wiring.jpg

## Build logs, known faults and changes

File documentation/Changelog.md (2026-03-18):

# Changelog

### Known issues:
- PWM mode may still not work, use version v9.11.0, if you want to use PWM mode

### Todo:
- Remove in vehicle files: XENON_LIGHTS, LED_INDICATORS, INDICATOR_DIR, doubleFlashBlueLight
- Add to EEPROM & select box: DOUBLE_CLUTCH and other transmission options

### 9.15.0-b2
- Track rattling optimized, many parameters adjustable in CaterpillarD6Dozer.h

### 9.15.0-b1
- Implementing dozer mode in progress, added #define TRACK_RATTLE_2 and #define HYDROSTATIC_TRACK_MOTORS in vehicle.h

### 9.14.0
- Documentation files in German added
- Documentation Files made by Frikkie Bester added
- Mercedes SK 1935 V8 truck added
- Mercedes SK 1838 V8 truck added
- Rough terrain crane added
- CRANE_MODE added (many hydraulic channels)
- SBUS can now decode 16 instead of 13 channels, used for additional servo outputs in rough terrain crane
- Hitachi ZW 370-6 wheel loader added
- FRSKY_TANDEM_HARMONY_LOADER remote profile added for TANDEM XE with touchscreen
- ESC settings added: HYDROSTATIC_MODE, directionChangeLimit
- Lights settings added: ROTATINGBEACON_ON_B1, INDICATOR_TOGGLING_MODE
- Audio2Header.html now including "reversing beep" category
- REVERSING_LOOP in the reversing beep file allows to use sounds with different start beep (see CATreversingBeep.h)
- Servo stroke limitation bug in EXCAVATOR_MODE fixed
- Hydraulic pump mixer added
- eeprom only active, if ENABLE_WIRELESS is defined (configuration website is enabled). This allows to change default values (for exampe servo positions) without changing the eeprom ID, if you don't want to use the website.
- Pingon 14C excavator added
- 7_Servos.h: SERVOS_HYDRAULIC_EXCAVATOR mode added. This allows to use non linear control curves for hydraulic valves, which eliminate the "dead zone" of most hydraulic valves. The curves are stored in curves.h. Also see servoCurves.xlsx
- Volvo EC550EL excavator sounds added
- CH 1 - 4 servo outputs now usable for bucket, dipper, boom and swing in EXCAVATOR_MODE, including simulation of virtual inertia
- 2 position switch on CH 5 allows to switch between ISO and SAE control pattern whithout changing the wiring (swapping dipper and boom channels)
- CAT 730 added

### 9.13.0:
- Defines removed: HAZARDS_WHILE_5TH_WHEEL_UNLOCKED
- Variables added (adjustable on 192.168.4.1): hazardsWhile5thWheelUnlocked
- Neopixel animation mode selectable in dropdown menu on 192.168.4.1
- Defines removed: NO_CABLIGHTS, NO_FOGLIGHTS, XENON_LIGHTS, FLICKERING_WHILE_CRANKING, SEPARATE_FULL_BEAM
- Variables removed: INDICATOR_DIR
- Variables added (adjustable on 192.168.4.1): noCabLights, noFogLights, xenonLights, flickeringWileCranking, swap_L_R_indicators, separateFullBeam, flashingBlueLight
- First light settings available on 192.168.4.1
- Website with collapsible sections to keep it more organized
- Servo positions adjustable on 192.168.4.1
- Improved website look
- Scania dashboard splash logo by Frikkiebester
- Dashboard requires less processing power, no engine rpm lagging anymore, if Frevic dashboard is used
- More adjustable ESC parameters on 192.168.4.1
- Dashboard improved & optional dashboard from Frevic implemented. Select it in "dashboard.h" by uncommenting "#define FREVIC_DASHBOARD"
- New parameter "#define NEOPIXEL_ON_CH4" in "6_Lights.h" allows to connect the NEOPIXELS to servo CH 4 (BUS mode only, no 5th wheel servo in this case)
- ESC parameters are adjustable via 192.168.4.1
- in "#define WEMOS_D1_MINI_ESP32" mode only: Experimental Serial command interface for ESC parameters

### 9.12.0:
- Support for 36 Pin version removed
- Support for Wemos D1 Mini ESP32 added (#define WEMOS_D1_MINI_ESP32 in "0_generalSettings.h").  Allows to use the upcoming wireless trailer controller as modular sound controller.
- In BUS communication mode: steering servo signal output stays disabled until auto zero was successful. Important in IBUS mode to prevent servo "ghost moves"
- Short triple flash, if no valid input bus signal is detected, no reboot loop anymore
- Short double flash, if no valid battery is detected, no reboot loop anymore
- WiFi Tx power adjustable in "0_generalSettings.h"
- Short double flash, if battery error during controller start
- WiFi Tx power lowered = less noise in the speaker and longer battery life
- Tx power is displayed in the serial monitor
- WiFi based configuration website for trailer options added
- Settings files renamed, "adjustments" removed
- ESP32 trailer software moved to (the old verion without WiFi is still included): https://github.com/TheDIYGuy999/wirelessTrailerESP32web

### 9.11.0:
- LS3 Engine added, used in James Bond Spectre Defender: Defender62LS3.h
- Changes in ESP32 trailer sketch. Mac addresses which are not working (causing engine revving issues) were discovered thanks to FrikkieBester. Unfortunately I still don't know why.
- In 7_adjustmentsServos.h: NO_WINCH_DELAY option added, servo signal for wincn is changed immediately in this case

### 9.10.0:
- First quick and dirty STEAM_LOCOMOTIVE_MODE implementation (see vehicles/Adler.h). Note, that you need to disable VIRTUAL_3_SPEED
- Steam whistle on horn channel
- In 8_adjustmentsSound.h: #define NO_INDICATOR_SOUND option, if you don't want the tic - tac sound

### 9.9.1:
- Flysky SBUS should now be stable with #define EMBEDDED_SBUS. Please let me know, if not.
- BATTERY_PROTECTION: scaling bug with higher resistor values fixed.

### 9.9.0:
- New NEOPIXEL_UNION_JACK animation for Land Rover ;-)
- New MAX_POWER_MILLIAMPS setting for Neopixels. This and other optimizations is eliminating the flickering Neopixels issue
- 3_adjustmentsESC.h: globalAccelerationPercentage allows to adjust the acceleration, if vehicle setting is not OK
- 4_adjustmentsTransmission.h: lowRangePercentage allows to adjust the acceleration in low transmission (off road) range. Used for MODE1_SHIFTING and WPL 2 speed transmission
- Channel failsafe changed
- 2_adjustmentsRemote.h: External SBUS library not required anymore. See option #define EMBEDDED_SBUS. "sbusInverted" moved to remote configuration profiles, so you don't have to change it anymore
- SBUS still unstable with Flysky remotes! Especially in combination with WIRELESS_TRAILER. Use IBUS in this case! I'm thankful for hints about this bug. Differences: Micro RC is sending an SBUS packet every 14ms, Flysky every 7ms

### 9.8.0:
- Adjustable RECOVERY_HYSTERESIS for battery protection
- 8_adjustmentsSound.h (masterVolumeCrawlerThreshold) and 3_adjustmentsESC.h (crawlerEscRampTime): switchable crawler mode with just minimal inertia for gearbox protection. Allows to have a "show mode" and a "competition mode"
- 3_adjustmentsESC.h: Additional comments in battery low dischgarge section, according to neo2001

### 9.7.0:
- NEOPIXEL_KNIGHT_RIDER scanner optimized, synchrone with sound
- NEOPIXEL_BLUELIGHT: red & blue bluelight animation for fire trucks etc.
- NEOPIXEL_HIGHBEAM: Neopixel bar now also usable for full beam and headlight flasher. Also working in combination with NEOPIXEL_KNIGHT_RIDER & NEOPIXEL_BLUELIGHT
- "Audio2Header.html" tool now able to remove noise in silent passages (option "remove noise floor")
- ESC state machine hanging in case 1 or 3, if throttle trigger direction changed qickly: bug solved
- Engine volume raising, if throttle trigger direction changed qickly: bug solved
- Improved ESC_DEBUG messages
- 3_adjustmentsESC.h: options better organized, OVERDRIVE now also usable with VIRTUAL_3_SPEED. In this case, the 4th (overdrive) gear is engaged @ full throttle & high RPM in 3rd gear
- 2_adjustmentsRemote.h: CHANNEL_AVERAGING option (recommended, if you have issues with unstable channels)

### 9.6.0:
- New version numbering: mainVersion.subVersion.patch It is also displayed in Serial Monitor, so you always know, which version you have on your vehicle
- "Out of fuel" voice message in many languages in "3_adjustmentsESC.h"
- Number of battery cells in series indicated by number of beeps after powering up the controller (#define BATTERY_PROTECTION mode only). This lets you always know, if your battery was detected properly.
- Knight Rider KITT scanner Neopixel animation now with sound (select it as siren in vehicle file). Scanner is now only on, if siren is on.
- Optimized "#define SEMI_AUTOMATIC" mode: Transmission is now downshifting earlier, if brake is applied

### 9.5:
- Battery low discharge protection options added to "3_adjustmentsESC.h". Used in combination with ESC's without protection or internal RZ7886 motor driver
- Battery level is shown on LCD dashboard (bottom left instrument and central display).
- Experimental "#define HIGH_SLIPPINGPOINT" option in "4_adjustmentsTransmission.h"
- New Defender V8 with open pipes
- clutchEngagingPoint lowered from 100 to 10 in several automatic transmission vehicles. This is standard.

### 9.4:
- Ticking noise, caused by accidentally enabled WiFi removed
- SBUS baudrate can now be fine adjusted in order to solve unstable channel issues, causing accidentally triggered indicators etc.
- Make sure you are using the latest version of my SBUS library!

### 9.3:
- Support for RZ7886 motor driver IC instead of classic RC ESC. Suitable for example for WPL vehicles with 370 motor. See "3_adjustmentsESC.h"
- New "brakeMargin" setting in "3_adjustmentsESC.h"
- ESC scaling bug of v9.2 fixed

### 9.2:
- Now compatible with latest Espressif Systems ESP32 board definition 1.0.6 (problem was caused by haedlights conflicting with TX pin)
- ESC now controlled by mcpwm (as all other servo outputs) instead of statusLED
- "Knight Rider" scanner for 8 Neopixels
- "b33lz3bub" Austria cab light animation for 3 Neopixels

### 9.1:
- New Benford 3 Ton Dumper sound
- New profile for the stick based "Micro RC" DIY remote. Allows to use remote CH 2 & 4 for other stuff
- New "#define SEMI_AUTOMATIC" option allows to use the 3 position switch for other stuff. The manual transmission is switched automatically

### 9.0:
- New parameter #define AIRPLANE_MODE in vehicle file (see MesserschmittBf109.h) for airplanes: throttle range always 1000-2000, idle @ 1000, no clutch simulation. No ESC output support, connect it directly to ESC!
- Added Frikkies ramps ESC mode to the ESP32 trailer sketch.

### 8.9:
- New parameter in 10_adjustmentsTrailer.h: TRAILER_LIGHTS_TRAILER_PRESENCE_SWITCH_DEPENDENT switches wireless trailer lights off, if no trailer is detected on truck mounted optional trailer detection switch on pin 32. If yo uwant to use this switch, comment out THIRD_BRAKELIGHT in 6_adjustmentsLights.h

### 8.8:
- Enabled Neopixels not conflicting with steering servo speed anymore, only executed every 20ms
- More Neopixel options, but still experimental
- High engine RPM is not heavily slowing down steering servo movements anymore
- #define HAZARDS_WHILE_5TH_WHEEL_UNLOCKED enables hazards, if 5th wheel is unlocked

- New SMD board with more connectors and switch mode power supply added
- Trailer software v0.3 with trailer leg support and light on / off switch, switched by tracrors 5th wheel

### 8.7:
- Trailer 5th wheel unlocking by servo CH4 can now also be used in combination with my "Micro RC" remote. Use "#define MODE2_TRAILER_UNLOCKING" in "7_adjustmentsServos.h"
- Kenworth sounds reworked
- New option for flickering lights during engine cranking in "6_adjustmentsLights.h": "#define FLICKERING_WHILE_CRANKING"
- New option for old vehicles with unsynchronised transmissions in "4_adjustmentsTransmission.h": "#define DOUBLE_CLUTCH"
- New vehicles: Saurer 2DM Swiss truck, Peterbilt with Detroit Diesel 8V92, Kenworth with open pipes CAT 3408

### 8.6:
- Magirus Mercur 125 air cooled V6 Diesel truck sound

### 8.5:
- ESP-NOW is only transmitting, if a variable in the packet has changed. Advantages: longer battery life, ESP32 stays cooler, less noise in the speaker
- Support for multiple trailer slaves (intended for articulated cattle trailer)
- support for trailer servos (legs, ramps, rotating beacon control). Controlled via horn pot (if hazards on / 5th wheel uncoupled)

### 8.4:
- Trailer software version for ESP8266 added
- German Magirus Deutz 256 V8 truck sound added
- Master volume scale is now logarythmic
- New options in "vehicle.h": "#define RPM_DEPENDENT_KNOCK", "minKnockVolumePercentage", "knockStartRpm" allow to adjust the knock volume depending on Engine RPM as well, not just depending on throttle input. A lot of vehicle sounds were optimised, using these options.

### 8.3:
- ESP-NOW based 2.4GHz wireless trailer lights control. Enable it in "10_adjustmentsTrailer.h". You can use a 2nd controller in your trailer as a slave.
- Trailer software can be found in "trailer/wirelessTrailer" for now.

### 8.2:
- Visual Studio Code can now be used as an Arduino IDE replacement. Libraries and board definitions are downloaded and configured automatically in this case.
- Important: "Rc_Engine_Sound_ESP32.ino" is now named "src.ino" and located in the "src" folder. See chapter "software" above
- Please note, that the folder structure has changed. For example the "Audio2Header.html" sound conversion tool is now located in the "tools" folder.
- All vehicle- & sound-files are the same as before and fully compatible.

### 8.11:
- Serious bug fixed: PWM communication mode was broken (thanks to Benny for reporting this issue)! -> Semaphore for multi tasking access to "pwmBuf" variable added, RTC watchdog timer changed
- Dashboard LCD: Jumpy instruments needle start animation bug fixed
- Tested wit Flysky FS-i6X in PWM mode and Micro RC in SBUS mode. Both including LCD dashboard.

### 8.1:
- Variable tire squeal, depending on steering angle and speed as well as during heavy braking
- See vehicle "MercedesActrosV6.h" race truck
- enable it with "#define TIRE_SQUEAL"

### 8.0:
- Automatic RPM lowering, if not digging for 5s in excavator mode
- new "dashRotation" variable allows to mount the dashboard LCD upside down: 3 = normal, 1 = upside down
- master volume bug fixed
- new Mercedes V6 FIA race truck sound

### 7.9:
- Hydraulic load dependent engine RPM drop for excavator mode
- Bucket rattle sound, if bucket or dipper stick moved fast

### 7.8:
- Caterpillar 323 Excavator sounds added including hydraulic and track rattling sounds
- Support for hydlaulic excavators (hydraulic pump, hydraulic flow, track rattling sounds). Use #define FLYSKY_FS_I6S_EXCAVATOR profile for remote
- I'm using it for my KABOLITE K336. Connect RX to the IBUS SERVO connector on the KABOLITE receiver

### 7.7:
- Support for 0.96 inch 80x160 st7735 LCD dashboard (details and wiring see "9_adjustmentsDashboard.h", thanks to Gamadril)
- Support for 2812 Neopixel LED (details and wiring see "6_adjustmentsLights.h", thanks to Gamadril)
- Support for Graupner SUMD protocol (thanks to Gamadril)

### 7.6:
- Actros sound optimised. More bass.
- More light options in "6_adjustmentsLights.h". Xenon etc. This is more convenient than inside the vehicle files.
- Servo output compiling error solved
- Support for rotating beacons control in "7_adjustmentsServos.h": #define CH3_BEACON. Connect this beacon to CH3 (BUS mode only): https://www.ebay.ch/itm/303979210629
- New "headlightParkingBrightness" option in "6_adjustmentsLights.h" allows to use the headlights as parking lights.

### 7.5:
- Support for non linear throttle and steering curves (for more accurate control around center position). Use "EXPONENTIAL_THROTTLE" & "EXPONENTIAL_STEERING" in "2_adjustmentsRemote.h"
- Support for HOBBYWING Quicrun Fusion Motor / ESC combo. Use "#define QUICRUN_FUSION" in "3_adjustmentsESC.h"
- support for winch, connected to CH3 (BUS communication mode only). Use "#define MODE2_WINCH" in "7_adjustmentsServo.h" The mode 2 button is then used to switch between horn / siren sontrol and winch control via CH4. The winch is controlled by an old RC servo driver board. The speed and neutral settings are done using "CH3L", CH3C" and CH3R" positions.

### 7.4:
- In "2_adjustmentsRemote.h": New remote profile for Flysky GT5 / Reely GT6 EVO / Absima CR6P (thanks to BlackbirdXL1 for making this profile)
- In "2_adjustmentsRemote.h": New remote profile for MT-305. This remote comes with the RGT EX86100 crawler
- "NO_SIREN" option. Siren is not triggered in this case
- "maxPwmRpmPercentage" lowered from 400 to 380 to prevent controller from random crashing in PWM mlode
- Microseconds channel signal range limited to 1000 - 2000. Required for RGT MT-305 @ full throttle dual rate

### 7.3:
- New Jeep Wrangler 392 HEMI V8 (bombastic with a good bass speaker!)
- Optimised V8 vehicles, using the new "RPM_DEPENDENT_KNOCK" (in vehicle file) option. This makes the engine sound way more realistic and aggressive @ high RPM. Ideal for "muffler deleted" vehicles.
- New "SERVO_DEBUG" option makes the servo calibration process easier. See "7_adjustmentsServos.h" tab"
- "VIRTUAL_3_SPEED" not interfering with automatic transmissions anymore
- "OVERDRIVE" option for 6 speed automatic transmission as well, not just for 4 speed. It's recommendet to leave it turned on, unless you have a double clutch vehicle.

### 7.2:
- "NO_CABLIGHTS" bug fixed
- US_Firetruck memory problem fixed
- Channel auto zero calibration reworked. See serial monitor, if you have issues. Never use "channelAutoZero = true" for unconnected channels or channels without spring centering!
- Indicators used as a debugger: the amount of blinks shows you the channel, which is not in neutral position (outside of 1400 - 1600 microseconds, check channel trim settings). Indicators constantly on means, that no SBUS signal is detected (check "sbusInverted" true / false in "2_adjustmentsRemote.h").
- Unimog U1000 with engine brake for Hermann

### 7.1:
- Servo output for shifting transmission now usable in combination with simulated automatic transmission. Use it as an off road reducer, don't shift it while driving fast or @ high engine RPM!

### 7.0:
- In "6_adjustmentsLights.h" tab: NO_CABLIGHTS" will skip the cablights step in the light control sequence, if defined. Use it, if your vehicle does not have cab lights. More light brightness options
- New "8_adjustmentsSound.h" tab for global sound options
- Vehicle specific configurations in "7_adjustmentsServos.h" allow to store servo endpoints for multiple vehicles. Useful, if the sound controller is used as an SBUS decoder.
- New Chevy 468 big block V8
- New Land Rover V8 with open pipes
- Adjustable reverse speed for automatic transmissions: "automaticReverseAccelerationPercentage"
- New "OVERDRIVE" option in "4_adjustmentsTransmission.h" allows to lower the engine RPM in 4th automatic gear
- BlinkLeds.ino sketch for LED test in /tools

### 6.9:
- New "JAKEBRAKE_ENGINE_SLOWDOWN" option, used in Volvo FH trucks with open pipe. If defined, the engine RPM is lowered, using the jake brake, while upshifting under full load as well as when the throttle is released quickly in neutral. You can hear it in this video: https://www.youtube.com/watch?v=MU1iwzl33Zw&list=LL&index=4
- New volvo FH with open pipes
- New GMC Sierra V8 Pickup with 3 speed automatic transmission
- A lot of new horn melodies from nenno

### 6.81:
- Third brakelight bug fixed
- Урал375 renamed to URAL375 (Windows is not able to read a mix of western and cyrillic letters)

### 6.8:
- "STEERING_RAMP_TIME" allows "scale" steering servo movements (BUS communication mode only)

### 6.7:
- MAN KAT V8 Diesel German Bundeswehr military truck for Onkel_Tom

### 6.64:
- Known issues added

### 6.63:
- Trailer coupling / uncoupling sound triggering switch debounced, correct sounds should now be played every time
- Typos in trailer sound playback section fixed

### 6.62:
- ESC state machine not locking up anymore, if "escBrakeSteps" is bigger than "pulseNeutral". This allows to achieve a more aggressive brake deceleration.

### 6.61:
- "'couplingSampleCount' was not declared in this scope" bug fixed

### 6.6:
- Trailer coupling & uncoupling sounds now triggered by a normally open switch, connected between pin 32 and GND. Intended to use the original TAMIYA switch.
- New "#define THIRD_BRAKELIGHT" setting in the "6_adjustmentsLights.h" tab. Comment it out, if you want to use the switch above.
- A trailer coupler (5th wheel) servo can now be connectet to the "CH4" header" (not available in PWM communication mode). See note (3 in "adjustmentsRemote.xlsx"

### 6.5:
- macOS Big Sur 11.x compiling error fix explained. See:  [Big Sur Fix](BigSurFix.md)
- Trailer coupling & uncoupling sounds in preparation, not yet working

### 6.4:
- CH1 & CH2 input pins can be used as PWM output for the steering servo and for the shifting servo. The outputs are active, if a BUS communication mode (SBUS, IBUS or PPM) is selected. This allows to use vers small "BUS-only" receivers. In this case, the servos are connected to the sound controller instead.
- Additional Servo adjustments parameters in tab "7-adjustmentsServo.h" added:
   - "SERVO_FREQUENCY" 50Hz is standard, some servos run smoother @ 100Hz.
   - Servo limits: left, center, right (allows to adjust both end points as well as the center point separately

### 6.3:
- Additional ESC adjustments parameters in tab "3-adjustmentsESC.h" added. Allows to optimise the HOBBYWING 1060 ESC, even if it has no internal adjustments parameters:
   - "escTakeoffPunch" adds more power, if accelerating from zero. Used, if your "clutch" is slipping too much while taking off.
   - "escReversePlus" allows to make the reverse speed faster (only, if "escPulseSpan" is more than 500)
- Additional "6_adjustmentsLights.h" tab:
   - "NO_FOGLIGHTS" will skip the foglights step in the light control sequence, if defined. Use it, if your vehicle does not have fog lights
   - "sideLightsBrightness" allows to adjust the brightness" of your parking lights / side markers
- New vehicle configurations like Diesel and petrol Landcruisers, generic 6 Cylinder Diesel (optimised for smaller speakers)

### 6.2:
- GAZ 66 redefinition bug fixed
- SMD version BOM error fixed
- Instructions PDF for ordering of pre assembled boards added
- STL data for SMD version bottom shell included
- Wastegate not triggered anymore while downshifting

### 6.1:
- SMD version tested
- "INDICATOR_SIDE_MARKERS" option: indicators are always on with dimmed brightness, if side markeers / parking light is on. This is often used in US trucks. See "KenworthW900ACAT3408.h" vehicle configuration
- You need to install the latest version of the "statusLED" library: https://github.com/TheDIYGuy999/statusLED
- Experimental new throttle array for heavy trucks in "curves.h" you need to comment / uncomment it manually for now.

### 6.0:
- Pig sound for Onkel_Tom ;-)
- Kenwworth W900A with CAT3408 made more aggressive (more bass) & alternative profile
- SMD version preview

### 5.9:
- LED PWM frequency is now 20kHz instead of 500 Hz. No PWM noise anymore in the speakers
- New "SEPARATE_FULL_BEAM" option. Wire your high beam lamps to the roof lights pin in this case
- New "INDICATOR_SIDE_MARKERS" option. Indicators are used as side markers as well in this mode

### 5.8:
- MAN TGX 680 vehicle profile
- SMD board v1.1, incl. Gerbers, BOM & Pick and Place file (still untestet)

### 5.7:
- Experimental support for virtual 16 speed sequential transmission "VIRTUAL_16_SPEED_SEQUENTIAL"
- New, alternative URAL-375D vehicle preset
- Indicators are now swichting on and off "soft" like incandescent bulbs, using an on and off ramp, if not defined "LED_INDICATORS" in the vehicle preset file. You need to use the latest statusLED update: https://github.com/TheDIYGuy999/statusLED
- New, untested SMD board version included

### 5.6:
- Horn & siren with variable length (as long as triggered). "Audio2Header.html" tool changed to add the required loop area (you need to adjust it manually) in the sound files.
- Horn & siren can play @ the same time
- New US fire truck (with CAT3408 V8 & Allison 6 speed automatic transmission) vehicle preset (use it to test the new variable length sounds)

### 5.5 (another big update):
- Way more flexible channel assignment, can easily be configured for my "Micro RC" remote, for a FLSKY FS-i6X or others. New "2_adjustmentsRemote.h" config file. You don't have to change the main code anymore in order to assign your channels. For details refer to "adjustmentsRemote.xlsx"
- New, state machine controlled lights control, if "#define AUTO_LIGHTS" commented out. Otherwise lights are controlled by the engine state
- New, optional xenon bulb ignition flash for headlights, if "#define XENON_LIGHTS" defined
- New option "#define ESC_DIR" allows to change the motor spinning direction in software
- New option "#define VIRTUAL_3_SPEED" lets you use the 3 position switch controlled 3 speed transmission, even if it doesn't exist ;-)
- Engine can be started manually by CH5 or automatically with the throttle stick (or the "momentary1" button on the "Micro RC" remote). Depending on setting "#define AUTO_ENGINE_ON_OFF"
- Serial communication mode for "Micro RC" remote removed (replaced with SBUS)
- Actions triggering rewritten, using updated rcTrigger library. You have to use the latest version: https://github.com/TheDIYGuy999/rcTrigger
- Added the missing "shifting" file type & german dropdown translations in "Audio2Header.html"
- Bug in Mack Super Liner configuration fixed
- IBUS interface tested, works fine, but "MAX_RPM_PERCENTAGE" > 350 will crash the ESP32. I recommend to use SBUS instead, because current Flysky firmware can generate SBUS signals as well.
- "MAX_RPM_PERCENTAGE" automatically limited according to communication mode. Required to prevent the controller from crashing (see above)
- In PWM mode, we can now read 6 channels
- PPM interface moved to RX pin, pins "35" & "PPM" are now used for PWM channels 5 & 6
- Bug fixed: wasteghate not triggered anymore while releasing brake rapidly
- Two-stage triggering for bluelight and siren, so we can use the bluelight separately
- Changing between jake braking and the normal engine sound is locked unless the current sample is looping back. This eliminates erratic klicking noises, if enabling or disabling the jake brake!
- To prevent issues with the mode buttons, you should install the latest software v3.5 on the "Micro RC" receiver
- If you use your own vehicle preset, you have to edit them, so that they use the same structure as the pre made ones. example: remove "const" in front of "uint32_t MAX_RPM_PERCENTAGE"
- New jake brake sounds for: Actros, URAL 4320, URAL 375D, Tatra 813 & M35. New dixie horn.

### 5.4:
- New: Volvo FH16 750, Dodge RAM 2500 with Cummins 12V
- "R6" knock pattern for inline 6 engines

### 5.3:
- PWM RC signal processing completely rewritten. It's now using the interrupt based ESP32 "rmt" core function rather than pulseRead(). Thanks to croky_b for the hint! No "MAX_RPM_PERCENTAGE" limitations anymore in PWM mode. 400% can now be used as well.
- PWM CH5 is now accessible on pin 35. This means, that the CH5 functions can also be used in PWM mode!
- Gear manual shifting sound not triggered anymore in automatic or doubleClutch mode. No need to disable it in automatic vehicles anymore.
- URAL4320, Unimog 1000 optimised
- New: Kirovets K700 V12 Diesel monster tractor with extreme turbo sound!

### 5.2 (a big update):
- New, comfortable .wato .h sound file converting tool ("Audio2Header.html" included). Based on bitluni's work
- Experimental Flysky IBUS support (see comunications settings, untested, you need to install this library: https://github.com/bmellink/IBusBM)
- New vehicle configuration structure: separate .h preset files for vehicles. Select them in "Adjustments.h". Makes vehicle selection a lot easier.
- Vehicle presets complely reworked. Most of them are now including a resound, which is seamlessly mixed together with the idle sound. Huge sound quality improvements!
- All vehicle specific presets and sound files are now located in "/vehicles"
- New vehicles: Defender Td5, VW Käfer, Actros 1863, SCANIA V8 trucks, URAL 375D, Jaguar XJS, MGB GT V8, Ford Powerstroke 7.3l V8 Diesel
- Idle and resounds are now throttle dependent es well, not just RPM dependent. Adjustable with "fullThrottleVolumePercentage". Useful, if you don't want to use the separate knock sound.
- "TOP_SPEED_MULTIPLIER" renamed to "MAX_RPM_PERCENTAGE", Max. engine RPM now adjustable in % of idle RPM instead of integer multiplier. Allows to do finer adjustments.
- "ADAPTIVE_KNOCK_VOLUME" renamed to "V8", added "V2" (these are ignition volume patterns for different engine types)
- "CATERPILLAR_MODE" renamed to "TRACKED_MODE" (for track based vehicles with dual ESC)
- new "SUPER_SLOW" option for very heavy, slow responding engines like locomotive diesels (see UnionPacific2002.h)
- "NumberOfAutomaticGears" setting moved from "curves.h" to "Adjustments.h"
- Gear ratio of 6 speed automatic transmission 1st gear changed, was too high
- Experimental pulseRead function (using interrupts) for PWM mode (disabled)
- Less aggressive RPM rise while downshifting the manual transmission
- Removed experimental "Multi slot knock samples", takes too much processing power in interrupt and does not sound good

### 5.1:
- Compiler warnings issue solved
- rcTrigger function moved to Core 1 (current Arduino IDE required, 1.8.7 does not work!)
- a lot of new functions (see below, triggered in "void rcTrigger()")
- Jake brake sound added (CH5, SBUS only) Uncomment //#define JAKE_BRAKE_SOUND, if you want to use it
- Headlight flasher and high / low beam switching added (CH5, SBUS only)
- Switchable master volume: indoor and outdoor mode (CH5, SBUS only)
- Switchable, virtual neutral for transmission, allows to rethe engine while standing still! (CH5, SBUS only)
- Kenworth W900A example configurations in Caterpillar 3408 (V8 4 stroke) and Detroit Diesel 8V71 (V8 2 stroke) version
- note, that you have to use the latest version of the rcTrigger library

### 5.01:
- Configuration mistake solved: "ADAPTIVE_KNOCK_VOLUME" (for V8) was not enabled in "Cat3408Settings" and *Master" setting"
- CAT 3408 Peterbilt added

### 5.0:
- The already existing "REV_SOUND" option is now fading over between the idle sound and the resound. This provides a very realistic behavior for heavy truck engines. Example see "Cat3408Settings", "Messerschmitt Bf109", "Unimog U1000". The fading threshold can be adjusted with the "revSwitchPoint" variable
- Optimized throttle fader for more realistic sound while gear shifting
- Optimised Wastegate triggering
- Optimised and new sound examples: Unimog U 1000 Turbo, Caterpillar 3408 (for King Hauler)
- Note, that only the "Master" settings example is listing all the .h files. Use this as a base for own settings

### 4.9:
- Ignition knock sound is now triggered by the optional revving sound as well
- Sounds and configuration example for Messerschmitt Bf 109 added (first example, which uses resound)

### 4.82:
- Missing .h files for the Ural 2 setting added
- Once again thanks to MAN Tgx for pointing out this issue

### 4.81:
- Bugfix: Several file names contained "Scanıa" (with Turkish i) instead of "Scania". This appears to be a problem under Windows but works fine under macOS
- Example configurations and .h files were reworked accordingly
- Thanks to MAN Tgx on the German RC Modellbau Portal for reporting this bug: https://www.rc-modellbau-portal.de/index.php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

### 4.8:
- Throttle fader for more natural knock behavior during take off
- Improved wiring and adjustments instructions down below
- New insanely loud supercharger sound option
- Example see "JeepCherokeeTrackhawkSettings" (use 6 gears in "curves.h)

### 4.7:
- Experimental support for my new rcTrigger library added
- Allows to trigger multiple latching and non latching actions per analog channel
- Note, that you have to install this library: https://github.com/TheDIYGuy999/rcTrigger

### 4.6:
- 75mm tank cannon fire sound and flash added
- Triggered via CH4
- Flash is using "Beacon 1" output
- Example settings: CATERPILLAR_MODE

### 4.5:
- CATERPILLAR_MODE (dual throttle input on CH2 & CH3 for tanks, diggers, bulldozers etc.
- No ESC control support in this mode! Wire two crawler type ESC (with direct brake) in partallel with CH2 & CH3 inputs, use dual headers)
- Example settings: CATERPILLAR_MODE_Settings (copy and paste it in "Adjustments.h")
- Also working in SBUS mode (allows to use additional sounds)
- New V12 tank sound from JPS952

### 4.4:
- Jeep Grand Cherokee Trackhawk added. Speaker with good bass reproduction needed!
- DAF XF truck added
- Adaptive knock volume added (the first knock per engine cycle will be louder, if defined "ADAPTIVE_KNOCK_VOLUME", adjust volume for others with "dieselKnockAdaptiveVolumePercentage" (see DAF XF settings)
- "Settings" files cleaned up

### 4.3:
- Simulated sequential double clutch transmission added. Variable "doubleClutch" in "Adjustments.h". See Ferrari setting (use 6 gears in "curves.h")
- Automatic transmission shifting strategy is now more robust, no oscillation anymore. See Chevy Nova V8 setting (use 3 gears in "curves.h")
- Knock sound for Chevy Nova V8 added. Sounds just great in combination with the 3 speed automatic transmission!

### 4.2:
- Dynamic, adaptive shift points for automatic transmission, depending on engine load allows economic driving
- Kick down detection will shift back, if instant full throttle is applied
- Replaced "sawtooth" arrays for automatic gear ratios with three one dimensional arrays for 3, 4 or 6 gears
- Reverse detection, only one gear in this case
- Gear ratios according to Allison datasheet (adjust reverse gear ratio according to your ESC reverse top speed)
- PROTOTYPE_36-PIN renamed to PROTOTYPE_36 to prevent compiler warnings
- Settings profiles for Ferrari & trophy truck with 6 speed automatic transmission & Chevy Nova with 3 speed automatic transmission added

### 4.12:
- Further automatic transmission fine tuning after big test drive with the Actros

### 4.11:
- Automatic transmission optimised in 1/14 scale Actros truck with Hobbywing 1080 ESC

### 4.1:
- Inspired by Wombii's fork of this repo: optimised simulated automatic transmission: load dependent "torque converter slip" added, optimised "4 speed sawtooth array", which is simulating the shifting points. Now we have 4 gears instead of 3, but you still can uncomment the 3 speed version array and use it instead. I recommend to use "automatic = true" in "Adjustments.h", if your RC vehicle does not have a real shifting transmission. My solution is way more simplistic than Wombii's, but still sounding good. Example settings see Land Rover and fire truck
- Harley Davidson optimised

### 4.0:
- Failsafe for SBUS now implemented and tested in the King Hauler build. The vehicle will do a controlled stop, if the SBUS wire is disconnected
- The SBUS failsafe flag from the receiver should in theory do the same, but I was not yet able to test it

### 3.9:
- Initial SBUS support on pin 36 "VP". Tested in combination with my "Micro RC" receiver (SW v3.4). Only one single signal wire required!
- It's working fine, but failsafe is not yet ready. Use it at your own risk!
- Use variables "SBUS_COMMUNICATION" & "sbusInverted" (changing signal polarity without an additional transistor) in "Adjustments.h" for configuration
- if you want to change the channel assignment, do it in readSbusCommands()
- Throttle overflow bug solved
- New, optimized Detroit Diesel mix for the KingHauler see "KingHaulerSettings2"

### 3.8:
- Experimental support for automatic transmission simulation. Use "automatic = true" to activate it
- Eagle schematic now including .brd PCB file -> upload it on www.oshpark.com to order your boards easily

### 3.7:
- "PROTOTYPE_36-PIN" allows switching headlights pin between D0 & TX0 pin. Required for the change to a 30 pin ESP32 board, which will be used on the final PCB.
- On the final PCB, the ESP32 will be powered from the ESC, the amplifier, the shaker and the LED from the on board 5regulator. This requires to remove the popping noise, which is generated, when the DAC offset of 128 is activated. So I added a fader for the DAC offset.

### 3.61:
- Tatra 813 V12 8x8 sound optimised
- New cooling fan & knock sounds

### 3.6:
- engine cooling fan sound added
- Scania 50 ton truck added
- Air cooled Tatra 813 V12 8x8 truck added

### 3.5:
- "dieselKnockStartPoint" variable allows to adjust the point where the volume of the knock sound is starting to increase
- Diesel knock sound triggering bug fixed
- Mercedes Actros & Harley Davidson sounds added
- Example files for vehicle specific settings added

### 3.4:
- Experimental support for separate engine revving sound. See "REV_SOUND" in Adjustments.h (don't use it)
- New Diesel ignition "knock" sound (fixed sample rate), played in synch with the engine sound (variable sample rate). This results in a way more realistic Diesel sound, because the ignition "knock" does not vary in pitch.
- engine sound is now mixed together from up to 4 sounds: idle, turbo, wastegate, Diesel knock. All of them are variable in volume, depending on throttle position or engine RPM. You can adjust everything, using a lot of variables in "Adjustments,h". The result is a very realistic engine sound. Allows to use an engine RPM range of 3 instead of 2 without sounding strange
- New squeaky brake sound
- Up to 11 sounds are now played in parallel!

### 3.3:
- Dimmed headlights during engine start
- International DT-466 sounds added
- New SCANIA V8 added
- Brake sound moved to the fixed sample rate playback interrupt
- Cleaned up playback interrupt functions
- DAC offset 128 moved to dacWrite()
- Brake sounds don't have to start & end @ -128 anymore
- Parking brake sound added
- Pneumatic shifting sound added

### 3.2:
- Added the new "Wastegate" sound. It is triggered, if the throttle is dropped rapidly
- Added Unimog U 1000, uses the new Wastegate sound
- Added AM General M35 truck

### 3.1:
- Added a new, pretty realistic SCANIA R620 "Straight Pipe" engine sound (ScaniaR620Uphill2.h). Pure goose flesh!
- Detroit diesel sounds with more bass added
- A speaker with good bass reproduction is required!

### 3.0:
- Ramping ESC signal faster below "clutchEngagingPoint" to prevent clutch from excessive slipping
- Solved a 2nd engine rpm bug during braking

### 2.91:
- Engine sound was slowing down too much during braking. This bug is now solved
- No turbo sound while braking: Bug solved
- King Hauler parameters fine adjusted
- "clutchClosingPoint" renamed to "clutchEngagingPoint"

### 2.9:
- "shiftingAutoThrottle" is altering throttle for synchronizing while shifting the TAMIYA 3 speed transmission -> Gearbox is protected, extreme realism in engine sound!
- More inertia added, engine idle volume lowered to 40%

### 2.8:
- "clutchClosingPoint" configuration variable added. Prevents engine sound from "rubber band effect". Engine sound is in synch (clutch engaged) with ESC power above this value
- Virtual clutch is also disengaging during gear shifting, allowing the engine rpm to settle down during shifting
- Acceleration speed now variable, depending on throttle position
- Added way more inertia to make vehicle behavior even more realistic
- Brake has now much finer granularity

### 2.7:
- Hornblasters train horns added
- Horns are now louder
- Trash removed
- Acceleratoin & deceleration now shifting transmission gear dependent

### 2.6:
- Indicator activation point adjustable with "indicatorOn"
- Norwegian siren, new air brake sound
- Door noise
- sound files moved to /sounds
- optimized bluelight patterns, using the new, optional "delay" variable. Latest statusLED library update required: https://github.com/TheDIYGuy999/statusLED

### 2.5:
- 3rd brake light on pin 32 added
- "escPulseSpan" > 1400 now working properly. Allows to accelerate and decelerate even smoother as well as limiting the top speed to a realistic level

### 2.4:
- Bug fixed: direct transition from state "braking backwards" to "driving backwards" now working
- failsafe function for serial signal added. Emergency brake is triggered in case of RC signal loss (serial & PWM mode only, PPM will follow)

### 2.3:
- Reversing light, reversing beep and brake light behaviour changed in order to interact correctly with the new vehicle mass simulation
- ESC is locked, if engine is not running ;-)
- Air brake sound now triggered correctly, as soon as the brake pedal is released
- I'm really amazed about this update! The vecihle almost behaves like a real truck now.

### 2.2:
- Support for crawler ESC (with direct brake) on pin 33. Vehicle mass simulation with proportional brake! Tested in Tamiya King Hauler (REELY Model No H0050 ESC) and working fine, but use it at your own risk! If you want to test it, connect ESC to pin 33 of the ESP32 instead of the receiver output.
- LED pins rearranged  to fit my board layout (you can change it in the pin assignment section)
- Scania R620 sound added

### 2.1:
- Additional turbo sound (playing in parallel with engine sound), volume and throttle dependent volume adjustable
- Caterpillar 3406B sound added
- VW Beetle sound added
- Indicator direction adjustable with "INDICATOR_DIR" = "true" or "false"
- Shaker rpm now adjustable for engine start, idle, full throttle & shutdown

### 2.0:
- Swiss post bus horn moved to category "sirens" ---> Replace existing .h file!
- Experimental ESC output (do not use it). Latest statusLED library update required: https://github.com/TheDIYGuy999/statusLED
- Mack truck sounds added

### 1.9:
- Kenworth W900 added
- Initial PPM signal input on pin 34 added. For now usable for steering and throttle signal. Uncomment "#define PPM_COMMUNICATION", if you want to use it.

### 1.8:
- LED pins changed for trailer light driver
- Horn sounds, siren sounds & additional sounds variable names changed! ---> Replace them all!
- Added more horns
- Added indicator (blinker) ticking sound
- Added independent volume adjustment for every sound
- Engine sound volume is now throttle dependent (adjustable)

### 1.7:
- Added shaker motor control on pin 23. Simulates engine vibration. IRLZ44N Mosfet and freewheel diode 1N5819 required
- Shaker power can be adjusted with the variables "shakerMin" & "shakerMax" in Adjustments.h
- Driver schematic down below
- I'm using a shaker motor from the G.T.Power kit 103061 (this controller is crap, but the accessories are useful)
- Foglight and side light pins moved to pins 18 & 19

### 1.6:
- Servo input channels rearranged to match the pinout of the "Micro RC" receiver (you can change it in the pin assignment section)
- Cleaned up the code a bit
- An updated version (16 timers) of my "statusLED" library is required: https://github.com/TheDIYGuy999/statusLED
- Added experimental support for serial communication with my "Micro RC" receiver: https://github.com/TheDIYGuy999/Micro_RC_Receiver
- Uncomment "#define SERIAL_COMMUNICATION" in Adjustments.h
- Connect pin 36 "VP" to pin "TXO" of the receiver (disable "TXO_momentary1" & "TXO_toggle1" in vehicleConfig.h)
- The "RC Servo Signals" are not required in this mode!
- Added Scania R500 V8 sounds

### 1.51:
- Solved issue: redefinition of 'const unsigned int sampleRate'

### 1.5:
- More Detroit Diesels added

### 1.4:
- Indicator (turn signal) support added
- RC signals now handled as arrays in order to simplify auto zero calibration of multiple channels

### 1.3:
- Irish fire truck horn
- Double flash blue lights option
- US fire truck air horn and air siren

### 1.2:
- Light functions added: reversing light, beacons (blue light), headlights, taillights with integrated brake lights
- My "statusLED" library is required: https://github.com/TheDIYGuy999/statusLED

### 1.1:
- Truck reversing beep sound added
- Can play in parallel with other additional sound and with variable speed engine sound!

### 1.0:
- Engine now slowing down, if switched off, not just fading out
- Fader bug fixed, now working smoothly
- HG P408 sounds added

### 0.9:
- Humvee Diesel engine sound added
- Truck pneumatic brake release sound added

### 0.8:
- volume offset bug was back and is fixed again!
- improved sound quality of Union Pacific 2002
- Detroit Diesel truck added
- Sine test tones added
- M2 sound added

### 0.7:
- fixed auto throttle zero calibration bug
- fixed "gap" bug, if sounds were triggered in PWM mode
- PWM mode now allows to trigger 2 sounds

### 0.6:
- fixed slow engine RPM response: The RC signal pulsewidth is now only read every 100ms, so much more processing time is available for other things

### 0.5:
- added idle sound volume adjustment variable "idleVolumePercentage" in "Adjustments.h"
- added Union Pacific 2002 SD70M 16 cylinder Diesel locomotive sounds
- added Jaguar XJS HE car sound (bad quality)
- added "pwmHornTrigger" variable in Adjustments.h", which allows to trigger the horn, using a PWM signal. Allows to use standard receivers

### 0.4:
- volume offset bug fixed
- added the typical Swisss post bus horn, an American police siren, a European Feuerwehr Martinshorn and a car horn
- added the varible "shifted", which allows to select between linear and shifted engine rpm response
- added schematic

### 0.3:
- Engine start / stop implemented, including starter sounds
- Three different start sounds available
- Horn implemented. It is played on pin 26 (see wiring instructions in code) triggered by switch on input 12
- Two different horn sounds available
- The horn can play in parallel with the variable speed engine sound!
- For easier access, the "settings.h" file was renamed in "Adjustments.h"

### 0.2:
- Many new 22'050Hz, 8bit sound files generated, mostly the same as in the ATmega 328 version, but in better quality :-)

### 0.1:
- Runs on an ESP32 (240MHz)
- It's still quick and dirty, but works with the included V8 short course truck idle sound
- sounds way better than the ATmega 328 version, thanks to  22'050Hz sampling rate (instead of 8'000Hz)

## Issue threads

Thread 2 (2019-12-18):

cannot compile with Arduino IDE

lubopetrov, 2019-12-18:
When compiling for ESP32
ISR (SPI_STC_vect) is showing as error with description
expected constructor, destructor, or type conversion before '(' token

TheDIYGuy999, 2019-12-18:
1. Install ESP32 boards
2. Select the correct board
3. Never select / uncomment more than one sound in the same category
4. Install the statusLED library (you need the update from yesterday) https://github.com/TheDIYGuy999/statusLED

pstorti, 2019-12-24:
**Arduino: 1.8.9 (Windows Store 1.8.21.0) (Windows 10), Board: "ESP32 Dev Module, Disabled, Default 4MB with spiffs (1.2MB APP/1.5MB SPIFFS), 240MHz (WiFi/BT), QIO, 80MHz, 4MB (32Mb), 921600, None"

C:\Program Files\WindowsApps\ArduinoLLC.ArduinoIDE_1.8.21.0_x86__mdqgnx93n4wtt\arduino-builder -dump-prefs -logger=machine -hardware C:\Program Files\WindowsApps\ArduinoLLC.ArduinoIDE_1.8.21.0_x86__mdqgnx93n4wtt\hardware -hardware C:\Users\Pedro\Documents\ArduinoData\packages -tools C:\Program Files\WindowsApps\ArduinoLLC.ArduinoIDE_1.8.21.0_x86__mdqgnx93n4wtt\tools-builder -tools C:\Program Files\WindowsApps\ArduinoLLC.ArduinoIDE_1.8.21.0_x86__mdqgnx93n4wtt\hardware\tools\avr -tools C:\Users\Pedro\Documents\ArduinoData\packages -built-in-libraries C:\Program Files\WindowsApps\ArduinoLLC.ArduinoIDE_1.8.21.0_x86__mdqgnx93n4wtt\libraries -libraries C:\Users\Pedro\Documents\Arduino\libraries -fqbn=esp32:esp32:esp32:PSRAM=disabled,PartitionScheme=default,CPUFreq=240,FlashMode=qio,FlashFreq=80,FlashSize=4M,UploadSpeed=921600,DebugLevel=none -ide-version=10809 -build-path C:\Users\Pedro\AppData\Local\Temp\arduino_build_857616 -warnings=none -build-cache C:\Users\Pedro\AppData\Local\Temp\arduino_cache_26355 -prefs=build.warn_data_percentage=75 -prefs=runtime.tools.esptool_py.path=C:\Users\Pedro\Documents\ArduinoData\packages\esp32\tools\esptool_py\2.6.1 -prefs=runtime.tools.esptool_py-2.6.1.path=C:\Users\Pedro\Documents\ArduinoData\packages\esp32\tools\esptool_py\2.6.1 -prefs=runtime.tools.mkspiffs.path=C:\Users\Pedro\Documents\ArduinoData\packages\esp32\tools\mkspiffs\0.2.3 -prefs=runtime.tools.mkspiffs-0.2.3.path=C:\Users\Pedro\Documents\ArduinoData\packages\esp32\tools\mkspiffs\0.2.3 -prefs=runtime.tools.xtensa-esp32-elf-gcc.path=C:\Users\Pedro\Documents\ArduinoData\packages\esp32\tools\xtensa-esp32-elf-gcc\1.22.0-80-g6c4433a-5.2.0 -prefs=runtime.tools.xtensa-esp32-elf-gcc-1.22.0-80-g6c4433a-5.2.0.path=C:\Users\Pedro\Documents\ArduinoData\packages\esp32\tools\xtensa-esp32-elf-gcc\1.22.0-80-g6c4433a-5.2.0 -verbose C:\Users\Pedro\Desktop\ENGINE\Rc_Engine_Sound_ESP32-master\Rc_Engine_Sound_ESP32\Rc_Engine_Sound_ESP32.ino
C:\Program Files\WindowsApps\ArduinoLLC.ArduinoIDE_1.8.21.0_x86__mdqgnx93n4wtt\arduino-builder -compile -logger=machine -hardware C:\Program Files\WindowsApps\ArduinoLLC.ArduinoIDE_1.8.21.0_x86__mdqgnx93n4wtt\hardware -hardware C:\Users\Pedro\Documents\ArduinoData\packages -tools C:\Program Files\WindowsApps\ArduinoLLC.ArduinoIDE_1.8.21.0_x86__mdqgnx93n4wtt\tools-builder -tools C:\Program Files\WindowsApps\ArduinoLLC.ArduinoIDE_1.8.21.0_x86__mdqgnx93n4wtt\hardware\tools\avr -tools C:\Users\Pedro\Documents\ArduinoData\packages -built-in-libraries C:\Program Files\WindowsApps\ArduinoLLC.ArduinoIDE_1.8.21.0_x86__mdqgnx93n4wtt\libraries -libraries C:\Users\Pedro\Documents\Arduino\libraries -fqbn=esp32:esp32:esp32:PSRAM=disabled,PartitionScheme=default,CPUFreq=240,FlashMode=qio,FlashFreq=80,FlashSize=4M,UploadSpeed=921600,DebugLevel=none -ide-version=10809 -build-path C:\Users\Pedro\AppData\Local\Temp\arduino_build_857616 -warnings=none -build-cache C:\Users\Pedro\AppData\Local\Temp\arduino_cache_26355 -prefs=build.warn_data_percentage=75 -prefs=runtime.tools.esptool_py.path=C:\Users\Pedro\Documents\ArduinoData\packages\esp32\tools\esptool_py\2.6.1 -prefs=runtime.tools.esptool_py-2.6.1.path=C:\Users\Pedro\Documents\ArduinoData\packages\esp32\tools\esptool_py\2.6.1 -prefs=runtime.tools.mkspiffs.path=C:\Users\Pedro\Documents\ArduinoData\packages\esp32\tools\mkspiffs\0.2.3 -prefs=runtime.tools.mkspiffs-0.2.3.path=C:\Users\Pedro\Documents\ArduinoData\packages\esp32\tools\mkspiffs\0.2.3 -prefs=runtime.tools.xtensa-esp32-elf-gcc.path=C:\Users\Pedro\Documents\ArduinoData\packages\esp32\tools\xtensa-esp32-elf-gcc\1.22.0-80-g6c4433a-5.2.0 -prefs=runtime.tools.xtensa-esp32-elf-gcc-1.22.0-80-g6c4433a-5.2.0.path=C:\Users\Pedro\Documents\ArduinoData\packages\esp32\tools\xtensa-esp32-elf-gcc\1.22.0-80-g6c4433a-5.2.0 -verbose C:\Users\Pedro\Desktop\ENGINE\Rc_Engine_Sound_ESP32-master\Rc_Engine_Sound_ESP32\Rc_Engine_Sound_ESP32.ino
Using board 'esp32' from platform in folder: C:\Users\Pedro\Documents\ArduinoData\packages\esp32\hardware\esp32\1.0.4
Using core 'esp32' from platform in folder: C:\Users\Pedro\Documents\ArduinoData\packages\esp32\hardware\esp32\1.0.4
Detecting libraries used...
"C:\\Users\\Pedro\\Documents\\ArduinoData\\packages\\esp32\\tools\\xtensa-esp32-elf-gcc\\1.22.0-80-g6c4433a-5.2.0/bin/xtensa-esp32-elf-g++" -DESP_PLATFORM "-DMBEDTLS_CONFIG_FILE=\"mbedtls/esp_config.h\"" -DHAVE_CONFIG_H -DGCC_NOT_5_2_0=0 -DWITH_POSIX "-IC:\\Users\\Pedro\\Documents\\ArduinoData\\packages\\esp32\\hardware\\esp32\\1.0.4/tools/sdk/include/config" "-IC:\\Users\\Pedro\\Documents\\ArduinoData\\packages\\esp32\\hardware\\esp32\\1.0.4/tools/sdk/include/app_trace" "-IC:\\Users\\Pedro\\Documents\\ArduinoData\\packages\\esp32\\hardware\\esp32\\1.0.4/tools/sdk/include/app_update" "-IC:\\Users\\Pedro\\Documents\\ArduinoData\\packages\\esp32\\hardware\\esp32\\1.0.4/tools/sdk/include/asio" "-IC:\\Users\\Pedro\\Documents\\ArduinoData\\packages\\esp32\\hardware\\esp32\\1.0.4/tools/sdk/include/bootloader_support" "-IC:\\Users\\Pedro\\Documents\\ArduinoData\\packages\\esp32\\hardware\\esp32\\1.0.4/tools/sdk/include/bt" "-IC:\\Users\\Pedro\\Documents\\ArduinoData\\packages\\esp32\\hardware\\esp32\\1.0.4/tools/sdk/include/coap" "-IC:\\Users\\Pedro\\Documents\\ArduinoData\\packages\\esp32\\hardware\\esp32\\1.0.4/tools/sdk/include/console" "-IC:\\Users\\Pedro\\Documents\\ArduinoData\\packages\\esp32\\hardware\\esp32\\1.0.4/tools/sdk/include/driver" "-IC:\\Users\\Pedro\\Documents\\ArduinoData\\packages\\esp32\\hardware\\esp32\\1.0.4/tools/sdk/include/esp-tls" "-IC:\\Users\\Pedro\\Documents\\ArduinoData\\packages\\esp32\\hardware\\esp32\\1.0.4/tools/sdk/include/esp32" "-IC:\\Users\\Pedro\\Documents\\ArduinoData\\packages\\esp32\\hardware\\esp32\\1.0.4/tools/sdk/include/esp_adc_cal" "-IC:\\Users\\Pedro\\Documents\\ArduinoData\\packages\\esp32\\hardware\\esp32\\1.0.4/tools/sdk/include/esp_event" "-IC:\\Users\\Pedro\\Documents\\ArduinoData\\packages\\esp32\\hardware\\esp32\\1.0.4/tools/sdk/include/esp_http_client" "-IC:\\Users\\Pedro\\Documents\\ArduinoData\\packages\\esp32\\hardware\\esp32\\1.0.4/tools/sdk/include/esp_http_server" "-IC:\\Users\\Pedro\\Documents\\ArduinoData\\packages\\esp32\\hardware\\esp32\\1.0.4/tools/sdk/include/esp_https_ota" "-IC:\\Users\\Pedro\\Documents\\ArduinoData\\packages\\esp32\\hardware\\esp32\\1.0.4/tools/sdk/include/esp_ringbuf" "-IC:\\Users\\Pedro\\Documents\\ArduinoData\\packages\\esp32\\hardware\\esp32\\1.0.4/tools/sdk/include/ethernet" "-IC:\\Users\\Pedro\\Documents\\ArduinoData\\packages\\esp32\\hardware\\esp32\\1.0.4/tools/sdk/include/expat" "-IC:\\Users\\Pedro\\Documents\\ArduinoData\\packages\\esp32\\hardware\\esp32\\1.0.4/tools/sdk/include/fatfs" "-IC:\\Users\\Pedro\\Documents\\ArduinoData\\packages\\esp32\\hardware\\esp32\\1.0.4/tools/sdk/include/freemodbus" "-IC:\\Users\\Pedro\\Documents\\ArduinoData\\packages\\esp32\\hardware\\esp32\\1.0.4/tools/sdk/include/freertos" "-IC:\\Users\\Pedro\\Documents\\ArduinoData\\packages\\esp32\\hardware\\esp32\\1.0.4/tools/sdk/include/heap" "-IC:\\Users\\Pedro\\Documents\\ArduinoData\\packages\\esp32\\hardware\\esp32\\1.0.4/tools/sdk/include/idf_test" "-IC:\\Users\\Pedro\\Documents\\ArduinoData\\packages\\esp32\\hardware\\esp32\\1.0.4/tools/sdk/include/jsmn" "-IC:\\Users\\Pedro\\Documents\\ArduinoData\\packages\\esp32\\hardware\\esp32\\1.0.4/tools/sdk/include/json" "-IC:\\Users\\Pedro\\Documents\\ArduinoData\\packages\\esp32\\hardware\\esp32\\1.0.4/tools/sdk/include/libsodium" "-IC:\\Users\\Pedro\\Documents\\ArduinoData\\packages\\esp32\\hardware\\esp32\\1.0.4/tools/sdk/include/log" "-IC:\\Users\\Pedro\\Documents\\ArduinoData\\packages\\esp32\\hardware\\esp32\\1.0.4/tools/sdk/include/lwip" "-IC:\\Users\\Pedro\\Documents\\ArduinoData\\packages\\esp32\\hardware\\esp32\\1.0.4/tools/sdk/include/mbedtls" "-IC:\\Users\\Pedro\\Documents\\ArduinoData\\packages\\esp32\\hardware\\esp32\\1.0.4/tools/sdk/include/mdns" "-IC:\\Users\\Pedro\\Documents\\ArduinoData\\packages\\esp32\\hardware\\esp32\\1.0.4/tools/sdk/include/micro-ecc" "-IC:\\Users\\Pedro\\Documents\\ArduinoData\\packages\\esp32\\hardware\\esp32\\1.0.4/tools/sdk/include/mqtt" "-IC:\\Users\\Pedro\\Documents\\ArduinoData\\packages\\esp32\\hardware\\esp32\\1.0.4/tools/sdk/include/newlib" "-IC:\\Users\\Pedro\\Documents\\ArduinoData\\packages\\esp32\\hardware\\esp32\\1.0.4/tools/sdk/include/nghttp" "-IC:\\Users\\Pedro\\Documents\\ArduinoData\\packages\\esp32\\hardware\\esp32\\1.0.4/tools/sdk/include/nvs_flash" "-IC:\\Users\\Pedro\\Documents\\ArduinoData\\packages\\esp32\\hardware\\esp32\\1.0.4/tools/sdk/include/openssl" "-IC:\\Users\\Pedro\\Documents\\ArduinoData\\packages\\esp32\\hardware\\esp32\\1.0.4/tools/sdk/include/protobuf-c" "-IC:\\Users\\Pedro\\Documents\\ArduinoData\\packages\\esp32\\hardware\\esp32\\1.0.4/tools/sdk/include/protocomm" "-IC:\\Users\\Pedro\\Documents\\ArduinoData\\packages\\esp32\\hardware\\esp32\\1.0.4/tools/sdk/include/pthread" "-IC:\\Users\\Pedro\\Documents\\ArduinoData\\packages\\esp32\\hardware\\esp32\\1.0.4/tools/sdk/include/sdmmc" "-IC:\\Users\\Pedro\\Documents\\ArduinoData\\packages\\esp32\\hardware\\esp32\\1.0.4/tools/sdk/include/smartconfig_ack" "-IC:\\Users\\Pedro\\Documents\\ArduinoData\\packages\\esp32\\hardware\\esp32\\1.0.4/tools/sdk/include/soc" "-IC:\\Users\\Pedro\\Documents\\ArduinoData\\packages\\esp32\\hardware\\esp32\\1.0.4/tools/sdk/include/spi_flash" "-IC:\\Users\\Pedro\\Documents\\ArduinoData\\packages\\esp32\\hardware\\esp32\\1.0.4/tools/sdk/include/spiffs" "-IC:\\Users\\Pedro\\Documents\\ArduinoData\\packages\\esp32\\hardware\\esp32\\1.0.4/tools/sdk/include/tcp_transport" "-IC:\\Users\\Pedro\\Documents\\ArduinoData\\packages\\esp32\\hardware\\esp32\\1.0.4/tools/sdk/include/tcpip_adapter" "-IC:\\Users\\Pedro\\Documents\\ArduinoData\\packages\\esp32\\hardware\\esp32\\1.0.4/tools/sdk/include/ulp" "-IC:\\Users\\Pedro\\Documents\\ArduinoData\\packages\\esp32\\hardware\\esp32\\1.0.4/tools/sdk/include/vfs" "-IC:\\Users\\Pedro\\Documents\\ArduinoData\\packages\\esp32\\hardware\\esp32\\1.0.4/tools/sdk/include/wear_levelling" "-IC:\\Users\\Pedro\\Documents\\ArduinoData\\packages\\esp32\\hardware\\esp32\\1.0.4/tools/sdk/include/wifi_provisioning" "-IC:\\Users\\Pedro\\Documents\\ArduinoData\\packages\\esp32\\hardware\\esp32\\1.0.4/tools/sdk/include/wpa_supplicant" "-IC:\\Users\\Pedro\\Documents\\ArduinoData\\packages\\esp32\\hardware\\esp32\\1.0.4/tools/sdk/include/xtensa-debug-module" "-IC:\\Users\\Pedro\\Documents\\ArduinoData\\packages\\esp32\\hardware\\esp32\\1.0.4/tools/sdk/include/esp-face" "-IC:\\Users\\Pedro\\Documents\\ArduinoData\\packages\\esp32\\hardware\\esp32\\1.0.4/tools/sdk/include/esp32-camera" "-IC:\\Users\\Pedro\\Documents\\ArduinoData\\packages\\esp32\\hardware\\esp32\\1.0.4/tools/sdk/include/esp-face" "-IC:\\Users\\Pedro\\Documents\\ArduinoData\\packages\\esp32\\hardware\\esp32\\1.0.4/tools/sdk/include/fb_gfx" -std=gnu++11 -Os -g3 -Wpointer-arith -fexceptions -fstack-protector -ffunction-sections -fdata-sections -fstrict-volatile-bitfields -mlongcalls -nostdlib -w -Wno-error=maybe-uninitialized -Wno-error=unused-function -Wno-error=unused-but-set-variable -Wno-error=unused-variable -Wno-error=deprecated-declarations -Wno-unused-parameter -Wno-unused-but-set-parameter -Wno-missing-field-initializers -Wno-sign-compare -fno-rtti -c -w -x c++ -E -CC
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

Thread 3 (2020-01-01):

converting sound files

pstorti, 2020-01-01:
im using the website to convert sound files, and all i get is static

care to help?

btw, why is there only one rev sound? where is it called upon?

TheDIYGuy999, 2020-01-01:
Are the included files working? If not, something is wrong with your wiring.

The rev sound is not yet implemented and for testing only.

pstorti, 2020-01-01:
Included files work just fine, even the huge 007 music, with great quality.
Only the ones I made are sounding bad

Followed the instructions to the letter

Em qua, 1 de jan de 2020 14:40, TheDIYGuy999 <notifications@github.com>
escreveu:

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

TheDIYGuy999, 2020-01-01:
You need a lot of practice to prepare good sounding idle files in Audacity. Important:
- only cut the files on the exact zero crossing points
- try to find the "repeating" pattern (you can "pre-hear" the marked area with shift & tab)

Closed 2020-01-13.

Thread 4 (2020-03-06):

2-speed manual gearbox support

AlfredBroda, 2020-03-06:
Adding 2-speed transmission support would be nice. In crawlers this would probably be a manual transmission (not throttle dependent). Having sounds and throttle managed while shifting would be very nice!

TheDIYGuy999, 2020-03-07:
a 3 speed manual is already supported, incl. sound & throttle management during shifting.

You jut have to change the shifting points (in ms) in gearboxDetection() to match your shifting servo:

// Gear detection
  if (pulseWidth[1] > 1700) selectedGear = 3;
  else if (pulseWidth[1] < 1300) selectedGear = 1;
  else selectedGear = 2;

AlfredBroda, 2020-03-07:
Ok, I'll look into it. Sounds like it only needs a different change channel to listen on. Does the throttle automatically ease off when `selectedGear` changes?

TheDIYGuy999, 2020-03-07:
The throttle is easing off, if you change to a higher gear and an additional throttle impulse is applied, if you change to a lower gear. This helps a lot to protect the shifting mechanism and sounds great. Have fun testing it!

Closed 2020-03-20.

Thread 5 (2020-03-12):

ideas: edits to wastegate trigger and dieselknock volume

Wombii, 2020-03-12:
While working with my automatic gearbox mod, I started reformatting the throttle calculations (mapThrottle() and engineMassSimulation() ) to make it easier to disable or modify parts of that code. These reformatted sections may or may not be useful to someone else, so I wanted to share it.
[throttleCalculations.txt](https://github.com/TheDIYGuy999/Rc_Engine_Sound_ESP32/files/4322175/throttleCalculations.txt)

By adding the contents of throttleCalculations.txt to a new tab and doing the following edit in the main tab, everything should work as it does in default version 3.4.

Replace:
```
    // Map pulsewidth to throttle
    mapThrottle();
    // Simulate engine mass, generate RPM signal
    engineMassSimulation();
```
with:
 ```
   //Throttle calculations (map, volume and mass)
   throttleCalculations2();
```

Note that turboOverPressureTrigger2(); contains an edit to more reliably trigger the wastegate sound and volumeCalculation2() contains an edit to change the diesel knock volume by both rpm and load.

Wombii, 2020-03-13:
I made a mistake in the diesel knock volume calculation in that file. Here's a working one with volume based on a combination of rpm and load, for the default 3.4 scania setup:
```
// Calculate throttle dependent Diesel knock volume
    //Temp variables are necessary to prevent interrupt from using unconstrained values
  int tempthrottleDependentKnockVolume;
  int throttleDependentKnockVolume1 = dieselKnockIdleVolumePercentage;
  int throttleDependentKnockVolume2 = dieselKnockIdleVolumePercentage;
  int throttleDependentKnockVolume3 = dieselKnockIdleVolumePercentage;

  if (!escIsBraking && engineRunning)
  {
    //First calculate knock based on rpm. More knock at higher rpms.
    tempthrottleDependentKnockVolume = map(currentRpm, 250, 400, dieselKnockIdleVolumePercentage, 110);
    throttleDependentKnockVolume1 = constrain(tempthrottleDependentKnockVolume,dieselKnockIdleVolumePercentage, 110);

    //Lower knock volume based on throttle input to reduce knock when dropping throttle.
    tempthrottleDependentKnockVolume = map(currentThrottle, 0, 450, dieselKnockIdleVolumePercentage, 70);
    throttleDependentKnockVolume2 = constrain(tempthrottleDependentKnockVolume,dieselKnockIdleVolumePercentage, 100);

    //Add extra knock based on difference between throttle and speed to simulate more knock when accelerating harder.
    tempthrottleDependentKnockVolume = map(currentThrottle-currentSpeed, 0, 500, 100, 500);
    throttleDependentKnockVolume3 = constrain(tempthrottleDependentKnockVolume,100, 500);

    //Calculate combined knock volume. Multiplying the values ensures knock volume is cut when releasing throttle.
    tempthrottleDependentKnockVolume = throttleDependentKnockVolume1 * throttleDependentKnockVolume3 / 100 * throttleDependentKnockVolume2/100;
    throttleDependentKnockVolume = constrain(tempthrottleDependentKnockVolume,dieselKnockIdleVolumePercentage, 100);

  }
  else throttleDependentKnockVolume = dieselKnockIdleVolumePercentage;

```

TheDIYGuy999, 2020-03-14:
Thank you for your feedback. I may include it in future versions

Closed 2020-07-07.

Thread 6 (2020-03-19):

Add RPM sensor support

artistru, 2020-03-19:
Hello. Your project is amazing! But i want suggest some improvements. For sport cars the best way to simulate engine sound, tones, sounds of virtual gear shifting is using real motor RPM instead throttle signal form receiver. For your arduino project i was modify the code to use HobbyWing RPM sensor, but in this project i have no skills to do this.
Do you have the desire and time to add support for this sensor?

TheDIYGuy999, 2020-03-20:
Good idea, but with the recommended crawler ESC you will not need it, because the RPM is in synch with the output signal.

Closed 2020-03-20.

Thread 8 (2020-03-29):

PCB: ESC with 6v BEC?

Wombii, 2020-03-29:
Are you designing the PCB to only support 5v BEC output, or will it be able to support 6v BECs as well?

TheDIYGuy999, 2020-03-29:
The ESP32 has its own on board AMS1117 3.3V regulator, which has an absolute maximum input voltage of 15V, so it should be no problem.

Closed 2020-04-05.

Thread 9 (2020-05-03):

D1 on PCB schematic not connected(not defined)

praji181, 2020-05-03:
hi there

I went through the schematic and i found that on the ESP32 30 pin board, D1( IO 1) is not connected to any point. i am sorry if i missed out anything, but can you clarify, if it is a problem with the schematic, or if that is a dummy(un used pin)

thank you

TheDIYGuy999, 2020-05-03:
Hi,
this is correct. You will have boot problems, if this pin is pulled down while powering up. For example, you can't drive an NPN transistor with 1k base resistor. So I moved the headlights to pin 0 for the 30 pin board.

Closed 2020-05-03.

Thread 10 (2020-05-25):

Suggestions/Doubts

praji181, 2020-05-25:
hi there, first of all let me thank you for this wonderful module you have created.  i use a GT PRO module and it is so limited. your work is awesome. Today successfully, i was able to connect everything to my truck and it worked like a charm, the sounds, the lighting and the dynamics. but there are some hiccups i came across, thought would let you know.

Just a few suggestions/doubts

1. I use a 6 channel 2.4Ghz box type transmitter. Can the channels or the stick be configured individually according to our preferences. ??
2.  Is there a way, to make the truck start at first using a channel( like GT PRO) and then it starts to roll when again an input on the stick is applied or stop it first, stays in idle and i get to turn the engine off manually.
3. I have an issue, when the forward channel is pressed the truck jumps first and then starts the engine. tried with the trimmers but no use.
4. can the lights and the horn be assigned switches, where we can turn it on and off, when we want. like turning on the hazard even though the truck is not on start mode, or leaving the headlights on even though the engine is not on. ( just an option)
5. turning on the engine and leaving the truck in idle and turning it off when we want is really a pleasurable thing to do. can you add that option as well.

But im not good with reading or interpreting the codes, maybe all these suggestions are already there in your code and i did not understand them or see them.

TheDIYGuy999, 2020-09-20:
Is your ESC connected to the ESC connector? Also note, that I don't recommend any other ESC than the Hobbywing 1080. I will work on the other topics, but it will take time. I have now ordered a Flysky stick based transmitter, so i can test this common setup.

TheDIYGuy999, 2020-10-08:
All your wishes are now implemented in v5.5

Closed 2020-10-08.

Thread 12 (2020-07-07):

General Questions

WarPorpoise, 2020-07-07:
Questions:
1. I noticed that some of the resistors in the pictures are blue indicating that they are probably metal-oxide resistors rather than the "typical" beige (carbon film) resistors. Can I use carbon film resistors, or are metal oxide resistors required?

2. Are 1/4 watt resistors sufficient for all "R" or should I use 1/2 watt (or more)?

3. Will BC337 NPN Transistors rated for 800ma & 45 Volt work for Q1-Q13?

4. Are the L, GND, R and +/- 5v connections on the PAM8403 soldered directly to the the connections on the board with some sort of jumper wire or are they soldered on pin connectors that are directly soldered to the board?

5. Does this appear to be the correct ESP32 dev kit for the newest 30 pin layout board?
[Amazon ASIN B07Q576VWZ](https://www.amazon.com/MELIFE-Development-Dual-Mode-Microcontroller-Integrated/dp/B07Q576VWZ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)
I have never worked with an ESP32, and I am having an extremely hard time telling which versions is correct.

6. I noticed in the YouTube videos that you had a different set of speakers running on your rigs vs. the linked speakers on YouTube and was wondering if you purchased these or built you own? They sound very accurate and seem to have good bass response for their size.

JPS952, 2020-07-08:
Warporpoise, I used 1/4 watt resistors, in fact half watts are too big to fit well on the board. I used the same ESP32's as in your amazon link. As for the Pam8403, just the  pins on the one side of the board are soldered through using header pins. The outputs to the speakers do not connect to the host PCB. I also used a big heavy speaker from Amazon in my project:  https://www.amazon.com/gp/product/B000230LBI/ref=ppx_yo_dt_b_search_asin_title?ie=UTF8&psc=1
this is an economical set of two speakers. I used one in my tank, check out JPS99 on Youtube.

TheDIYGuy999, 2020-07-08:
1. It does not matter
2. Any 1/4 Watt resistor will work
3. OK
4. Use 2.54mm male pin headers, directly soldered
5. OK
6. They are from this kit: https://www.banggood.com/Original-G_T_POWER-Lighting-And-Voice-Vibration-System-For-4WD-Tamiya-Tractor-Truck-RC-Car-Parts-p-1296706.html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

pavlosweb, 2020-07-27:
Did you try to add integrated wifi support or or bluetooth LE control? Perhaps web interface to make some settings?
I am very gratefull for your work. I am trying to build my own RC based on your code. It works like a charm. But when I try to use wifi or BLE it crashes. It has to do something with HW timers. When disabled it works well but I do not have suffient knowledge why is that or how to fix it. It seems you are in pretty good knownlege about esp32, do you have any idea?

TheDIYGuy999, 2020-07-27:
Yes, I tried to add WiFi upload, but it never worked properly. I think, enabling WiFi just takes too much resources. It's not on my priority list at the moment. I prefer to invest time in sounds. I'm also working on improving the additional functions triggering, using my new rcTrigger library.

pavlosweb, 2020-07-27:
> Yes, I tried to add WiFi upload, but it never worked properly. I think, enabling WiFi just takes too much resources. It's not on my priority list at the moment. I prefer to invest time in sounds. I'm also working on improving the additional functions triggering, using my new rcTrigger library.

I found similar issue https://www.reddit.com/r/esp32/comments/an8z16/how_to_move_timerbegin_interrupts_to_the_other/ It seems it is possible somehow. Dou you think I could get rid of hw timers and do its code in loop with appropriate delay or it is complete nonsense?

I understand it is not your priority. Thank again for awesome work.

TheDIYGuy999, 2020-07-27:
I'm already using both cores. The timers are required for led control as well as for mills() and micros().

delay() is always nonsense in my opinion and probably the most stupid thing in there Arduino world.

Closed 2020-08-26.

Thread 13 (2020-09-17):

Tankmotorsound-2.h doesn't work properly with RC_Engine_Sound_ESP32.ino V5.1

JPS952, 2020-09-17:
I was behind in software revs  and went from Version 4.6 to 5.1.  I loaded the Actrox3363 settings as a baseline and uploaded them and they seemed to work okay.  I then changed the start sound to  tankstart3.h and that worked okay too.  I then added my Idle sound "tankmotorsound-2.h" and uploaded it and testing gave weird results.  While idling there is a loud repetitive1 hz knocking sound and the idle sound repeatedly revs up at about a 4hz rate.  I have gone back to the 4.6 version of software for now as it does what I need. If you would like to hear the sound let me know. jsangemino@yahoo.com

TheDIYGuy999, 2020-09-18:
If you make new sounds in Audacity:
- search for a cyclic pattern in the idle sound (the amount of ignition pulses is usually the same as the cylinder number), cut the "idle" sample to exactly this length, have a close look at the zero crossings to avoid clicking noises. The loudest peak should always be at the end of the sample.
- do the same with the "rev" sound. It will be 2 - 4 times shorter than the "idle" sample, depending on the engine and rpm of the "rev" sample
- Change the "Rate" (dropdown on the left of the sample) of the "rev" sample, until the length is the same as in the "idle" sample. This is very important!
- copy a part of the "rev" sample (the one with the original, unchanged "Rate" speed). This is the "knock" sample. Cut it to this max length: "Idle" length / number of cylinders / rpm range "MAX_RPM_PERCENTAGE" (usually 2 - 4 or 200 - 400%)
- Knock sound settings:
-- "dieselKnockInterval" = number of cylinders
-- uncomment "V8" for V8 engines or "V2" for V2 (Harley) engines
-- adjust "dieselKnockAdaptiveVolumePercentage" (how loud the "silent" knock pulses are compared with the loud ones), only active, if selected V8 or V2
- play with the other volumes, start-, end- and switch-points until you are happy
- The "rev" sound is optional and only active, if "REV_SOUND" is defined (// removed)
- Adjust the transition from the "idle" to the "rev" sound, using "revSwitchPoint", "idleEndPoint", "idleVolumeProportionPercentage". This step is very important and can make a huge difference!

I will add these informations to the v5.2 documentation. v5.2 will also include an optimised, pre made IS-3 tank sound preset

JPS952, 2020-09-18:
Thanks very much for the quick and detailed response and the updated version of software. I will apply the changes today. I appreciate how you have continuously updated and improved your software on all your projects!

Closed 2020-09-18.

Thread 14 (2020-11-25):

Indicator L always ON

tedisusilo, 2020-11-25:
Sorry Sir,my rc sound with ESP32 DEV KIT led indicator left always On,and shaker not running,,thats it
Many thanks

tedisusilo, 2020-11-26:
Uncomment //#define AUTO_INDICATORS
Fixed

Closed 2020-11-26.

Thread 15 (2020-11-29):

Indicator L always blinking

tedisusilo, 2020-11-29:
Transmitter DumboRC X6 ESC DumboRC 10A pair ESP32 30 pin
Indicator lost signal always ON (indicator L) but all channel function normally,,3days I search and editing sketch but not working,,work if I delete all function off indicator L
Please help me to fix this issues Sir
Many thanks

tedisusilo, 2020-11-29:
Indicator lost signal ON because power of the battery is low..
Thanks

Closed 2020-11-29.

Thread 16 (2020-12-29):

V. 6.1 Servos don't work

Frenazo, 2020-12-29:
Hi.
thank you so much for this amazing project.
I have a board with version 6.1 installed, connected by Sbus and all sounds, lights and motor work perfectly, however I can't get the servos to work connected to the PCB board terminals. If I connect the servos directly to the receiver they do work. Attached photo of the connections.
Thanks a lot.
P.D .: I am Oscar Moreno oscarveterinario from youtube, xD
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

TheDIYGuy999, 2020-12-30:
Hi Oscar,
thanks for the praise. This behaviour  is normal. You can't connect the servos to the ESP32 board in SBUS mode, there are no RC signal outputs. The only exception is the ESC output. This means, you have to connect the servos directly to the receiver.

Frenazo, 2020-12-30:
Thanks!

Closed 2020-12-30.

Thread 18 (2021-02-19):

Fuse

Frenazo, 2021-02-19:
Hello Martin.

As always: GREAT JOB!!!

You recommended to use a fuse between the battery and the sound controller / ESC, ¿what kind of fuse?

Thanks

TheDIYGuy999, 2021-02-19:
Hi,
the easiest solution is a car fuse in the battery + wire. Rating as low as possible, depending on the size of your car.

Frenazo, 2021-02-19:
Thanks
5A is enough or is it too much?

TheDIYGuy999, 2021-09-25:
Depends on you motor and ESC

Closed 2021-09-25.

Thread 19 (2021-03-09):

5V use from BEC ?

Skirmitt83, 2021-03-09:
Hi, Is there a specific reason there is a 5V voltage regulator used  on the board instead of the 5V BEC ?
Also a small hint to use a LDO regulator that works from around 5.5 - 6V.
Just ordered the SMD PCB :-)

babajun12, 2022-11-07:
Indeed, I attached an ESC with 6V BEC and fried the sound amplifier module while I bridged the BEC voltage to the +5V terminal.

Closed 2023-02-01.

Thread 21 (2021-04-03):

compilation error

klimma1508, 2021-04-03:
Hello, I tryed to uploatd Your program to esp32, but it write that error. Where can be probem? Thank you Klimš
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

TheDIYGuy999, 2021-11-07:
Install all required libraries according to the documentation

Closed 2021-11-07.

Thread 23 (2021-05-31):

Issue increasing throttle hard instead of slowly from remote

Riffer, 2021-05-31:
When increasing throttle slowly the system works, but if I push the trigger hard, the ESC throttle increases to a point of no return and even the sound still outputs the full system is completely unresponsible.

Tried with different Frameworks (compiled with PlatformIO)
I use FlySky. Remapped channels for my GT4 Evo.

To get an impression, please see this video: https://www.youtube.com/watch?v=AR_BHpd-OOI

Riffer, 2021-05-31:
In the meantime I found out, with PWM the problem does not appear - seems related to IBus?

Riffer, 2021-05-31:
Progress: I changed the handler of IBus from polling (in your loop you only do it every 10 ms, the documentation of IBus library says, do it every ms!? ) to interrupt and now the throttle works:

 iBus.begin(Serial2, 3, COMMAND_RX, COMMAND_TX); // begin IBUS communication with compatible receivers

I see you have only the timers 0 and 1 in use for the sound mixer, why don't you let IBus do the job with another timer? Or did I miss something?

Closed 2021-11-07.

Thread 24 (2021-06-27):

Sound issues across different gearboxes

Whitey092, 2021-06-27:
Hi Martin,

Thanks for all your hard work, Love this project!

I've just updated to this latest version using the mercedes actross engine file. Normally I use the simulated 3 speed transmission, however it seems the engine does not 'rev up' to its limit. It sounds more dull or like its stuck in high gear. I makes the gear change noise when I actuate the switch but doesn't seem to change.

The 16 speed makes the correct engine noise, but I prefer the 3 speed.

Any chance you know what the fix would be?

Regards,
Sam

Whitey092, 2021-08-06:
So it appears it’s just the virtual 3 speed gearbox. It won’t rev up like the others do. How do we fix this?

TheDIYGuy999, 2021-11-07:
It should be fixed now

Closed 2021-11-07.

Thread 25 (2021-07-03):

Question: add some functions

klimma1508, 2021-07-03:
Hello, can you add to your program controlling tank with one joystick, add kickback and output to servo? I tried myself, but I’m bad in programming, so I can’t do it and your program is closest to what I need. Thank you. Klimš

tonyc770, 2021-09-02:
Is there a jet engine sound, startup and throttle like the others?

Thanks,
Tony

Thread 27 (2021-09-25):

Questions about PWM input

ws786873, 2021-09-25:
I used a 6ch PWM receiver and only connected CH3. In the software, I selected a remote controller recommended to use PWM communication settings, and annotated all types and models to use PWM. But I can't get the sound. What's wrong with me. When I use debug mode, it seems that channel detection cannot cycle. It always shows that channel 1 is out of the set range.

TheDIYGuy999, 2021-09-25:
Make sure, that "channelAutoZero" is set to "false" for all channels which are unconnected or don't have spring centering

ws786873, 2021-09-25:
I set all channels except 3CH to false in adjustmentremote, and my horn finally sounded, but it only increased output at 0-5% duty cycle and decreased output at 6% - 10%. 11% - 89% output idle sound, 90% - 100% is the same as 0-10%. I can see the throttle reading in the monitoring window. Most of the time, it is 0. So  is there any problem

TheDIYGuy999, 2021-09-25:
Looks like your throttle CH range is not 1000 to 2000 microseconds ( = -45 to 45° servo movement), which is standard. "Check your transmitter settings. You may want to lower "pulseSpan". What does "CHANNEL_DEBUG" say?

ws786873, 2021-09-25:
I can't understand what ch range is and why its unit is microseconds. In my understanding, it is a 0-3.3v square wave. I measured the output frequency of the receiver with a multimeter, which is 49hz, channel_ Debug say: the throttle value changes between 1099-2099. When my throttle is actually about - 40 ° - 40 °, channel_ Debug's throttle is displayed as 1599, which I think is a center position. In this way, the problem is too large a middle range. And I have a complete positive and negative range at the beginning and end.

TheDIYGuy999, 2021-09-25:
This is just how it was specified. Your throttle center position should be 1500. If not, "channelAutoZero" is not enabled or you touched the throttle during the initialization. Then it should work properly.

Closed 2021-11-07.

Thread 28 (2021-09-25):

Sound and flashing light

Frenazo, 2021-09-25:
Hi,
The sound and light control has been working perfectly in tests with a simulated light board. I have installed everything in a Tamiya Actros and my surprise is that the sound plays normally if the lights are off, but if I turn the lights on the sound jumps when accelerating and the lights blink.
The lights are fine if the engine is not revved.
I use a 5,000mAm 7.2V NiMH battery, may I need a 3S Lipo (11.1V)? Thank you.

Regards

TheDIYGuy999, 2021-09-25:
Hi, I believe, that your 5V regulator is overloaded and cutting out, if the lights are on and the amplifier needs more current during revving. Are you using the original SMD board or what type is your regulator? Are you using series resistors for all LED? Maybe you want to post a picture of your setup?

Frenazo, 2021-09-25:
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

TheDIYGuy999, 2021-09-25:
Please answer the questions

Frenazo, 2021-09-25:
Sorry.
The board is JLCPCB (not SMD).
I have mounted 2 SMD boards from JLCPCB and for some reason there is no communication between the ESC and the Receiver.

"Are you using series resistors for all LED?", Yes, sure, 1 resistor for each led

This is the provisional board and work perfectly:

https://www.youtube.com/watch?v=LIhg95roQEs

Frenazo, 2021-09-25:
The regulator is the BEC in Hobbywing 1080

TheDIYGuy999, 2021-09-25:
These could be potential issues:
- bad solder joint
- wiring error
- wrong series resistor
- 1000 uF capacitor soldered wrong way around

The regulator can't be the Hobbywing ESC BEC. Its voltage (6V) is too high for the amplifier and it will burn out. You need a 5V regulator on the board for the amplifier and for the LED.

Frenazo, 2021-09-25:
Ok.
The regulator in board is this: https://www.banggood.com/10pcs-L7805CV-TO220-L7805-TO-220-7805-LM7805-MC7805-Original-IC-p-1070097.html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

The board is the same in test and final truck, then I think "bad solder joint" is less probably.
Then I see "wiring error" or "wrong series resistor" first.

Thank, I'll try and we speak!

Frenazo, 2021-09-25:
Solved!
The problem was the potentiometer, I lowered the volume by turning the screw and it has been solved.
I sacrifice a few decibels to make everything work.
Thank you!!

Regards, Óscar

Frenazo, 2021-09-25:
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

Closed 2021-09-26.

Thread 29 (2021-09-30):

Buzzer for electric vehicle

furetec, 2021-09-30:
Hello,

I have an electric car that is too quiet.
I would like to equip it with your ESP32 engine sound.
Your circuit would be controlled by a potentiometer on the accelerator pedal.
Do you think this is possible?
If yes, how?

Thank you

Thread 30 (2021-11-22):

SMD Board Not Working

Whitey092, 2021-11-22:
Hi Martin,
I can’t seem to get the smd boards working, I’ve had a batch made from 2 different suppliers including PCB way. I’ve checked all the pre soldered components and all are correct.
When powered on the esp 32 lights up but I cannot get it to do anything else. However putting the same esp 32 board in the original PCB it runs without a problem.
Am I missing something or is this a known issue?
Thanks for your help!

TheDIYGuy999, 2021-11-22:
Hi,
this not a known issue. I'm assuming there is a polarity issue with a diode or with an ULN2003. Did you check the voltage on the 5V rail, which is supplied by the on board 7805 regulator?

Whitey092, 2021-11-23:
Polarity all ok. 5V rail all good. I seem to have figured it out, SBUS needs to be inverted on smd boards. Does this sound right? Thanks for your help! Keep up the great work with this project! I love it!

Closed 2021-11-23.

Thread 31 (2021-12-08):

Enable mapping WS2812 leds to functions

VynDragon, 2021-12-08:
Currently they are just  RGB hue decoration.
Enable mapping WS2812 leds to functions like indicators, high beams, cabin lights, etc.

TheDIYGuy999, 2023-03-01:
Other functions were added

Closed 2023-03-01.

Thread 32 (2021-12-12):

Cannot get it to compile on platform.io

sascha-schieferdecker, 2021-12-12:
Problem seem to be related to FASTLED and fastpin:

 #define _FL_DEFPIN(PIN) template <> class FastPin<PIN> : public _ESPPIN<PIN, ((uint32_t)1 << (PIN % 32)), _FL_PIN_VALID(PIN)> {};
                                                                                                                             ^
.pio\libdeps\esp32dev\FastLED\src/platforms/esp/32/fastpin_esp32.h:154:17: note: in expansion of macro '_FL_DEFPIN'
 _FL_DEFPIN(56); _FL_DEFPIN(57); _FL_DEFPIN(58); _FL_DEFPIN(59);
                 ^
.pio\libdeps\esp32dev\FastLED\src\platforms/esp/32/fastpin_esp32.h:136:125: error: template argument 3 is invalid
 #define _FL_DEFPIN(PIN) template <> class FastPin<PIN> : public _ESPPIN<PIN, ((uint32_t)1 << (PIN % 32)), _FL_PIN_VALID(PIN)> {};
....

There are many more compiler errors like that. Is this a known problem?

sascha-schieferdecker, 2021-12-12:
Well, for anyone else stumbing across this problem, I could get a build if not using FASTLED 3.4.0, but 3.3.3.

I modified the platformio.ini like this:

`lib_deps =
    SPI
    https://github.com/TheDIYGuy999/statusLED
    https://github.com/TheDIYGuy999/SBUS
    https://github.com/TheDIYGuy999/rcTrigger
    https://github.com/bmellink/IBusBM
    https://github.com/Bodmer/TFT_eSPI
    https://github.com/FastLED/FastLED/archive/refs/tags/3.3.3.tar.gz`

sascha-schieferdecker, 2021-12-12:
Maybe the platformio.ino should have some version pinning in the lib_deps, so that only working versions are provided as dependency

TheDIYGuy999, 2021-12-15:
I added it in platformio.ini, but for me 3.4.0 is working as well

Closed 2022-04-22.

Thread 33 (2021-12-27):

Restart loop. Not a power issue

lolren, 2021-12-27:
My ESP32 loops at Initializing SBUS, check transmitter & receiver (sbusInverted true / false OK?)... then spits out some gibberish. nothing happens

TheDIYGuy999, 2021-12-28:
If you want to use SBUS, change sbusInverted true / false or vice versa. Also make sure, your receiver is powered up

lolren, 2021-12-28:
I did. Still nothing. But the problem is actually the restart of the ESP32. Sometimes it doesn't restart and has a different message, but the receiver is still not recognized, no mother what. Will try to order a new ESP32, but this one works with another projects.

TheDIYGuy999, 2021-12-29:
and you are using ESP32 board definition version 1.04 as mentioned in the sketch?
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
Otherwise it will crash.

lolren, 2021-12-31:
Yes. That`s the problem. Unfortunately, V1.04 is old enough an we cannot buy it, so the solution would be to see where the problem is and, if it`s not a vital function maybe disable it or change it. My board is 1.05 and I've ordered a 1.1 , and I`m still getting the same issue. The problem is that you cannot pick what board definition you buy, is kinda a lucky dip.
Ive notice that the restart loop goes away if I change the platform definition to a newer one (eg. espressif32@3.4.0) but then, ~I get another error, like ([E][WMath.cpp:74] map(): Invalid map input range, min == max), so the code must be changed and adapted to the newer boards definitions.

Regards

lolren, 2021-12-31:
I have tried to disable each library, one by one ( and the functions associated with them) in the code. Finally, when I disabled the watchdog  function the board stopped restarting. Now, I don`t know yet if the board is frozen and doesn't restart, or it will work, More investigation is needed. Regards

TheDIYGuy999, 2021-12-31:
v1.04 is not related to the hardware. It's the board definition, provided by espressif. You have to use 1.04:
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

lolren, 2022-01-04:
Hi. Sorry for the late reply, been busy with the new year😁
I've installed v1.04 , but this didn't change anything. Still getting weird restarts after a few seconds, related to watchdog.
Now I think my remote control protocol is not supported
But this is ok, as I'm building the unit for a friend of mine that uses a Flysky.

Thank you

lolren, 2022-01-05:
Managed to fix the restart loop issue, by disabling the watchdog.
But, now with a FLYSKY_FS_I6X  , I cannot get the board to sync for some reason. CH 1 signal out of auto calibration range, check transmitter & receiver is the error I get, no matter what I choose from the remote option. Regards

TheDIYGuy999, 2022-01-05:
If you have a valid SBUS signal coming in, you don't have to disable the watchdog. Looks like your steering CH1 is not in center position:
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

lolren, 2022-01-15:
You can close the issue. The problem was, indeed the  ESP32 board definition above 1.04.
Also the reason that the remote didn`t sync was that I had no idea the receiver must have  SBUS output.
I was stupidly trying to connect to the PWM output.
Thank you for the support.
Regards

fiechr, 2022-02-19:
I assume, that I have the same issue (using PlatformIO)

The platform parameter in the platformio.ini is set to "platform = espressif32@3.0.0"

Some LEDs are blinking and the speaker makes a popping noise every few seconds. The serial monitor repeats the same message about S-BUS initialization endlessly every few seconds.

This is my first board, so in addition I also don't know what it is supposed to do.

I've tried multiple receivers, PCBs and ESP32 dev boards. I also tried inverted/non-inverted.

But it seems to have nothing to do with that.

lolren, 2022-02-19:
It's the receive. You need a speci ibus or sbus receiver. That solved my problem. Regards

fiechr, 2022-02-19:
I've tested a Flysky FGr4v2 (with NB4 radio), an A8S and a iA6B (with I6 radio), as well as a Radiolink R7FG.

All receivers were set to SBUS mode in the RX settings.

lolren, 2022-02-19:
But, did you connect the esp to the SBUS output, not a PWM output?

fiechr, 2022-02-19:
I'm pretty sure, yes. Some have dedicated SBUS output pins, others use ports like "SERVO" or "IBUS".

Is there any way to get more information on why it fails exactly? Is it possible to configure the radio or its configuration wrong, so it reproduces this kind of issue? I will check out the debug settings on the *.ino file.

I've tried different radios with my own settings and also the I6 with the stock I6X profile, but still, no SBUS initialization.

fiechr, 2022-02-19:
After trying different setups and hardware, I finally tried set `sbusInverted` again and now it works...
Maybe a combination of different settings.

The FrSky FGr4 and iA6B seem to use inverted SBUS signals.

Closed 2022-04-22.

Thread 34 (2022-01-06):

Mutex type semaphores cannot be used from within interrupt service routines.

sp3esu, 2022-01-06:
Hi.

While working on my modification of Sound Engine I got an issue that while reading some I2C sensors software crashed. After a small investigation, I found that the I2C driver fails in using semaphore. I found such note in the documentation: ["Mutex type semaphores cannot be used from within interrupt service routines."](https://docs.espressif.com/projects/esp-idf/en/latest/esp32/api-reference/system/freertos.html)

After removing semaphore usage in the interruption handler function everything is working fine.
https://github.com/TheDIYGuy999/Rc_Engine_Sound_ESP32/blob/4f940f085a6c04f4c201149b9e84758c03eb0ac3/src/src.ino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

Replace xSemaphoreCreateMutex with xSemaphoreCreateBinary is not making any change - software is still crashing.

This can lead to other unexpected issues, so I suggest changing the way how channels data is synchronized. I didn't figure out it yet by myself. If I find a way I'll create PR.

Best Regards!
Gregor

Schrottschrauber, 2024-12-15:
Hello,
when integrating the I2C DAC MCP4728 to control a power servo I also get constant RESETS.
The initialization works fine, but I get resets when outputting the speed.
Can you tell me exactly what you have changed so that it works?

I am grateful for any help

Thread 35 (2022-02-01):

Boat sounds help

lolren, 2022-02-01:
Hi. I`m sorry to open this thread as an issue, but I cannot find another way for help. Me and my friend got the truck sounds working, and now we are struggling to add boat sounds. We understand the Audacity and converter part, but we don`t really understand the accelerating part. Is this a different sound? does it speed up the sound? we have to add a idle sound as well as an accelerating sound? Please help :D Kind regards,

Loren

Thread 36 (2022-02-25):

Use throttle range from 1000-2000 with no reverse gear

derFrickler, 2022-02-25:
Is it possible to configure the throttle range from 1000-2000 such as motor off is at 1000 and full throttle is at 2000
No reverse gear needed.

This would be great for models (airplanes) that don't have reverse gears.
Any hints on how to use this would be great.
So far i am using PWM input with all channels but Throttle/3 set to NONE.

TheDIYGuy999, 2022-03-05:
Done in v9.0

derFrickler, 2022-03-05:
Thanks! I got it working already with a dirty fix directly in the readPWM
`
int offs = (pulseWidth[3]-1000)/2;
pulseWidth[3] = 1500+offs;
`
Will Update to 0.9 then.
BTW, is there a way to stop the engine via PWM signal? Maybe if going lower than 1000?

Closed 2022-03-05.

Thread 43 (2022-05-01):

Use with Single core CPU

Akash-MuPhile, 2022-05-01:
Can ESP32-S2 be used for this code? It probably has higher pin count

TheDIYGuy999, 2022-05-30:
No, it can't be used

Closed 2022-05-30.

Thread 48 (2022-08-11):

PCBWay component help

BusDriverLee, 2022-08-11:
I've tried to order the boards using the files section with PCBWay, but they have quoted the incorrect SMD-ECAP-10x10 for C1. They have quoted part number EEE-1AA102P which is too big. I believe it should be EEEFC1A102AP but this has a different stamp compared to your picture examples. Any help with the correct part number would be much appreciated.

fiechr, 2022-08-12:
Looking at the Digikey database these two seem to have the same size (dimensions and value). Both are 10x10 mm and 1000µF. Also the footprints look identical (same dimensions). Only different series and longer lifetime.

https://www.digikey.de/de/products/detail/panasonic-electronic-components/EEE-1AA102P/766035
https://www.digikey.de/de/products/detail/panasonic-electronic-components/EEE-FC1A102AP/1141901

Or am I missing something? What do you mean with "too big"?

BusDriverLee, 2022-08-12:
[FileFromPCBWay.xlsx](https://github.com/TheDIYGuy999/Rc_Engine_Sound_ESP32/files/9316714/FileFromPCBWay.xlsx)
Hi @fiechr,
Thank you for your quick reply. Please see attached the spreadsheet that was sent to me by PCBWay. They are stating that the components they have will fall off the board. Hopefully this sheet will make sense to you as it doesn't to me! I wonder if they have been sent the wrong component?

fiechr, 2022-08-12:
I have to agree, that the pads are pretty short and I also had some difficulties when hand-soldering the capacitor on my own PCBs.

On the other hand, the footprint should be big enough. I don't know why they now reject it, since, I assume, others have ordered the PCB including assembly in the past successfully. Other SMD components, like linear voltage regulators or transistors also use contact areas below the actual device. In this case the whole PCB needs to be heated up, because there is no other way to make the solder flow in between.

The caps I used (see image below) have the same size they show in the picture inside the spreadsheet file. It's pretty tight, but works.

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

Without changing the footprint on the board itself, I think, the only way is to either solder the capacitor later yourself by hand or replace it with a smaller one, so they accept it, even if it most likely will have a lower capacity, it should still be fine for this application.

BusDriverLee, 2022-08-23:
Hi @fiechr,

Thank you for your help. I managed to find an 8mm that seems to have the same specifications - EEE-FT1A102GP. I have sent this to them and they have assembled a board. I am awaiting delivery so I can try it out..... fingers crossed!

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

Lee

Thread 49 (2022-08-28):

Enabling RZ7886 ESC Breaks most sounds

VynDragon, 2022-08-28:
Version: Github Clone and 9.10.0 zip

As title says. On latest from Github version and 9.10.0, Enabling the RZ7886 ESC breaks most sounds (engine rev up, turn signal, breaks... only basic engine sound works) and prevents restarting the engine with the stick hold function with Flysky 6 Channel remote (and keeps model immobile after turning off engine with same function)
Tested on controller by itself with just receiver, power, and sound,  and in full setup with RZ7886 ESC.

VynDragon, 2022-08-28:
Tested and Happens with 9.3 too. Issue doesnt happen with SBUS, only IBUS.

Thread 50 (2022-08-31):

question: a different way to change the engine speed

fisenkodv, 2022-08-31:
Is it possible to use the Hall sensor to emulate the engine speed instead of RC controller? The idea is I have a bike's wheel and based on the wheel rotational speed change the sound of the engine. Any ideas, links, etc. are appreciated.

isopix, 2023-01-07:
Hall sensor?

Simple "Proximity Sensor" (using magnet too, but digital. It doesn't need analog or precision at all).

Closed 2023-02-01.

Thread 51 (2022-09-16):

Board rebooting with latest ESP Board versions

SalmanSheikIsmail, 2022-09-16:
Board reboots when the Arduino code is compiled using ESP32 board versions after 1.0.5.

Faberonline, 2023-02-28:
> Board reboots when the Arduino code is compiled using ESP32 board versions after 1.0.5.

Is there a fix??? I have the same problem... Is it the bootloader or ..?

TheDIYGuy999, 2023-03-01:
Currently, there is no other fix than using board version 1.0.5

Closed 2023-03-01.

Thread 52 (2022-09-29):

small version for 1:43 cars(Siku Racing)

isopix, 2022-09-29:
Hi,

When looking on your PCBs with microUSB connector, they look huge. Speakers are even larger than your PCBs

I have collection of Siku Racing cars (1:43 scale).

I don't need anything(lights, etc), beside engine sound. But wonder if such board+speaker would fit if there will be installed IR transponder already:

http://www.miniz-forum.de/siku-racing-mercedes-mit-robitronic-transponder-ausstatten-t26876.html
http://www.miniz-forum.de/userpix/3786_Mercedes_SLS_2.jpg
http://www.miniz-forum.de/userpix/3786_Anschluss_1.jpg
http://www.miniz-forum.de/userpix/3786_IMG_2390_2.jpg
http://www.miniz-forum.de/userpix/3786_IMG_2394_1.jpg
http://www.miniz-forum.de/userpix/3786_IMG_2395_1.jpg

https://www.youtube.com/watch?v=N1-xgpxS_rg

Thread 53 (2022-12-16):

Tank mode

SJoWie80, 2022-12-16:
Hello

If i use it in tank mode en add the 2 esc to ch2 en ch3 on the esp pcb it doesnt work. I hear the sounds etc but the esc do not respond am i doing something wrong?

Regards
Joey

TheDIYGuy999, 2023-03-01:
Tank mode does not support ESC output. You have to control them directly from your transmitter

Closed 2023-03-01.

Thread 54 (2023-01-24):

Compilation error while uploading

Draxuxe, 2023-01-24:
Hello,

When I use Arduino IDE to transfer your code to the esp32, there is a bunch of compilation error popping up : "Compilation error: redefinition of '...'" and i only uncommented one .h for my vehicles.
Thanks for the help

fet43, 2023-02-16:
good job I already copied the code but it always gives the same error was it possible to help ??

In file included from c:\Users\acer\Documents\Arduino\libraries\FastLED\src/FastLED.h:75,
                  from C:\Users\acer\Desktop\files\sun\Rc_Engine_Sound_ESP32\src\src.ino:99:
c:\Users\acer\Documents\Arduino\libraries\FastLED\src/fastspi.h:157:23: note: [#pragma](https://www.youtube.com/hashtag/pragma) message: No hardware SPI pins defined. All SPI access will default to bitbanged output
  # pragma message "No hardware SPI pins defined. All SPI access will default to bitbanged output"

TheDIYGuy999, 2023-03-01:
redefinition means you uncommented multiple options at the same time.

No hardware SPI pins defined. can be ignored

Closed 2023-03-01.

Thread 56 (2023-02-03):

PWM

racin44, 2023-02-03:
I'm having issues getting the code changed from ppm to pwm. any help would be appreciated.

rengels, 2023-09-10:
you have to modify 2_Remote.h and switch off everything that is not PPM.

This one works for me: https://github.com/rengels/Rc_Engine_Sound_ESP32/blob/huracan/src/2_Remote.h

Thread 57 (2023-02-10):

sound issues

racin44, 2023-02-10:
This is my second soundboard of this and the only sound i get is clicking. The only difference is I'm using less of the setup, Lighting. This is for a rc race car. I been trying multiple esp32 boards to see if that's the issue, but its not.

TheDIYGuy999, 2023-02-13:
What does the serial monitor say?

racin44, 2023-02-13:
A2      : 0x00000000  A3      : 0x00000005  A4      : 0x3ffbdcf4  A5      : 0x00000000
A6      : 0x00000005  A7      : 0x00000001  A8      : 0x3ff59064  A9      : 0x3ff59000
A10     : 0x00000000  A11     : 0x3ffc3b88  A12     : 0x3ffc3b88  A13     : 0x00060623
A14     : 0x00060620  A15     : 0x00000001  SAR     : 0x00000018  EXCCAUSE: 0x00000006
EXCVADDR: 0x00000000  LBEG    : 0x4008501d  LEND    : 0x40085025  LCOUNT  : 0x00000027

Backtrace: 0x400d61f6:0x3ffdd710 0x400d3e47:0x3ffdd740 0x400d3249:0x3ffdd760 0x400d2493:0x3ffdd780 0x400d2c9f:0x3ffdd7b0

ELF file SHA256: 36f1d3323bc41389

Rebooting...

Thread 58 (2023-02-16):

Hobbywing 1060 esc will not arm

VelocityAddiction, 2023-02-16:
My 1060 will not arm when connected to the Board through PWM. I have an older board that had code from 2 years ago. I connected that board to my truck and everything worked normally. The esc armed and ran. Once flashed with the newer code it no longer armed and worked. Unfortunately I searched for the older files on my computer and could not find them. I flashed with the oldest version available on github but still would not arm. Wired everything directly to my Rx and everything worked. Confirmed its some sort of code issue but can't track down what setting is causing it.

TheDIYGuy999, 2023-03-01:
What does the Serial monitor say?

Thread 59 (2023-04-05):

Control issues volume dependant

Whitey092, 2023-04-05:
Hi Martin,
I’m having an issue with control dependant on volume.
There is no issue when at maximum and 1 notch down.
At lowest and muted volume levels any speed/throttle/brake settings are ignored. The ESC accelerates as if it is not controlled by the board, will not brake and has no inertia.

I made a new board with a new esp32 just to rule that out but it didn’t make a difference.

FBester1976, 2023-04-05:
Hello,

The board is put in "Crawler mode" based on values in 8_adjustmentsSound.h. So, in crawler mode the virtual inertia is disabled.

If you do not want Crawler mode, you need to make the **masterVolumeCrawlerThreshold** less than the lowest Volume percentage you have. If you make the masterVolumeCrawlerThreshold = 43 or less, you will not have Crawler mode for the current selection below.

// Volume adjustment
const  uint8_t numberOfVolumeSteps = 3; // The mumber of volume steps below
const uint8_t masterVolumePercentage[] = {100, 66, **44**}; // loud, medium, silent (more than 100% may cause distortions)

//const  uint8_t numberOfVolumeSteps = 4; // The mumber of volume steps below
//const uint8_t masterVolumePercentage[] = {100, 66, **44**, 0}; // loud, medium, silent, no sound (more than 100% may cause distortions)

// Crawler mode
const uint8_t **masterVolumeCrawlerThreshold** = **44**; // If master volume is <= this threshold, crawler mode (without virtual inertia) is active

Hope this helps...

TheDIYGuy999, 2023-04-06:
Thank you, Frikkie!

Whitey092, 2023-04-24:
Ahhh perfect! Thank you.
I have one more question.
When using Virtual 3 Speed and wireless trailers, the truck engine sound goes to full rev as soon as you start the truck. If I move the throttle a little bit it comes back down. But with throttle at neutral it revs high. Am I missing something that controls that?

FBester1976, 2023-04-24:
Some basic questions:

What remote do you use?
Do you have a self-centring spring on the throttle?
Do you always switch the remote on before the truck?
Possible to make a video? Youtube link?

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

Whitey092, 2023-04-28:
Hi Frikkie,
Thanks for your response. I am using Flysky Paladin EV. Self centering sticks, and yes transmitter always powered on before reciever.

As I said this only happens with wireless trailers enabled. If I uncommonly wireless trailer it works perfectly.

Here is a YouTube short link:
https://youtube.com/shorts/ncpT9OmvEzY?feature=share

I have tried it with trailers connected also but it does not fix the problem.

Closed 2023-04-06.

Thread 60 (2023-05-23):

Simple ESP32+PAM8403+FS-IA6B no sound

Radh62, 2023-05-23:
Dear Sirs, owner and contributors,
Thank you for your fine activity on RC sound modules!
After a succesful implementation of your Arduino based RC sound module on a G scale Steam locomotive (with my own sounds and tweaks), an attempt to use an ESP32 based sound module was made. Just the ESP32 board (without the shield from PCBWay, nor other), the PAM8403 amplifier and a receiver (FS-IA6B with Flysky - I6 transmitter) in the prototypical layout (the project requires relatively small dimmensions and physical flexibility).
Since I want to use the board with receiver's PWM signals, I commented all #defines in communication section, kept the Flysky definition on remote.h and activated by uncommenting the autoengine on_off. I put throttle signal CH3 from the receiver to pin 13 and signal CH2 from the receiver on pin 12 (like in your pictures). Pins 25 and 26 were connected to PAM8403 like in Readme.md. The code uploaded OK with the recommended settings (no errors), but there is no sound when the throttle or horn are activated. I get only a repetitive weak "scratching" noise synchronous with the blinking LED (and I guess the blinking should not be active). Power LED  (the other, not blinking LED) is lit OK. I scoped the throttle signal connected to ESP board and is normal and clean at approx. 3.3V which means that pins 12 and 13 are on input state (high impedance). Then another ESP32 board was tested with the exact same result. The serial monitor returns random characters (on 9600 baud and several other rates) for both boards.
A helping hand to push me on the right path would be very much appreciated since I do not know what to do anymore, I'm not skilled with programming and I very much like the project.
Best regards!

TheDIYGuy999, 2023-05-24:
Hi, please read the comments in this file carefully: https://github.com/TheDIYGuy999/Rc_Engine_Sound_ESP32/blob/master/src/2_Remote.h
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
In general I recommend to use IBUS with your receiver. The transmitter needs to be configured according to:
https://github.com/TheDIYGuy999/Rc_Engine_Sound_ESP32/blob/master/documentation/adjustmentsRemote.xlsx

For a locomotive use "vehicles/Adler.h" as an example. It includes #define STEAM_LOCOMOTIVE_MODE, which is important.
Hope this helps

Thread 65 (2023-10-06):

BOM.xls in gerbers.xls

ArchWinDoors, 2023-10-06:
I have followed the How to Order from PCBWay, received assembled board - Just wondering why many of the components are struck-out: e.g WAGO SREW CLAMP.
These components missing, means that I don't have everything I need to set up and finish the board.
Basically the BOM included differs from what's shown at: https://youtu.be/csQgTfxRd8Y?t=102
I'm novice so I didn't know items were missing when PCBway sent the confirmation..
PCBWay have followed the files sent to them and I can't really raise a dispute if they've followed the BOM.xls sent from the repo.

FBester1976, 2023-10-06:
Hello,

If I understand you correctly, you are missing all the through hole components?

In the video and on the instruction (https://youtu.be/csQgTfxRd8Y?si=0IE6IQnMq7uUKS0f&t=75) they speak about SMD (Surface mount) and through hole components. If you ordered according to the video and the instructions, you would have specified no through hole components.

You need to order those components separately from a supplier in your area.
***@***.***
SMD assembly from PCBWay
***@***.***

After I soldered all the through hole components. (as the YouTube video explains)
***@***.***

Below are just some links so you can see what you need (not sure if you are also planning the wireless trailer card?)

PAM8403 5V Amp, x1 truck  sound card, none on trailer card.
https://www.amazon.in/ICSTORE-PAM8403-Amplifier-Speaker-Subwoofer/dp/B07HLB1HMR

5pcs MP1584 5V Fixed Output 3A DC Step Down Converter Buck Module 4.5-28V Input x2 (needed for truck and trailer)
https://www.jacobsparts.com/items/DCMOD-I-5V

RAMPS PCB CONNECTOR SCREW TYPE x2 (needed for truck and trailer)
https://www.diyelectronics.co.za/store/connectors-wiring/296-ramps-pcb-connector-screw-type.html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

20K Ohm 203 Multi turn Trimpot Potentiometer / Variable Resistor, (x1 truck  sound card, none on trailer card.)
https://electrobes.com/product/20k-ohm-203-multi-turn-trimpot-potentiometer-variable-resistor/

SINGLE ROW 40-PIN 2.54MM PITCH PIN HEADER (RED, BLUE, YELLOW, WHITE OR BLACK)  I prefer coloured pins, makes plugging in easier.
https://hobbycomponents.com/connectors/741-single-row-40-pin-254mm-pitch-pin-header-red-blue-yellow-white-or-black

1×40-Pins 2.54mm SIL Female Header (if you can get 15-pins, you do not have to cut the 40-pin)
https://handsontec.com/index.php/product/40-pins-sil-female-headers/

ESP32 Dev board 30PIN x2 (needed for truck and trailer)
https://www.walmart.ca/en/ip/Loewten-ESP32-Development-Board-WiFi-ESP32-Development-Board-ESP32-Development-Board-Module-30-Pin-2-4GHz-WiFi-2-In-1-Microcontroller-Pr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

Regards,

Frikkie

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

TheDIYGuy999, 2023-10-07:
Thank you, Frikkie

ArchWinDoors, 2023-10-09:
@FBester1976 Thank you, this makes sense now and I appreciate the links to source equivalent components.

Closed 2023-10-09.

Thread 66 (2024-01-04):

pinmapping

lazu020, 2024-01-04:
I want help. I am using esp board, but this board not have some pins. Where can i find pinmapping for remap.
Thanks for help.

rengels, 2024-01-04:
The pin mapping depends heavily on the compile flags.
You can however see a lot on the HW layout.

My proposal: save some effort and just order the correct board. They are cheap enough that it's just not worth to fiddle around with the SW to remap the pins.

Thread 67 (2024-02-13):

Sound

ryadavoi, 2024-02-13:
Hello, I only need sound for my project on esp32 arduino ide, but I can’t get just the code for sound

rengels, 2024-02-14:
The header files containing the sounds are what you need then.

On my branch there is a tool to convert the header files back to wav files: https://github.com/rengels/Rc_Engine_Sound_ESP32/blob/huracan/tools/Header2Audio.html

If you want to use the sounds on an arduino you would need to convert them back again.

ryadavoi, 2024-02-18:
I don’t need sound files, i need library for sound playback , without motors, leds and others

rengels, 2024-02-18:
Then this is not your project.
It uses way to much HW if you just want to play sound.

I googled something for you:
https://www.arduino.cc/reference/en/libraries/soundplayer/

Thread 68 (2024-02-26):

Engine sound controlled by Analog input horn controlled by digital input

vinhx, 2024-02-26:
Hello sir,
your project so great!
I'm currently making an 3 wheels electric bike for my children. that the motor speed controlled by a hall sensor , the signal output is analog 0 to 5v. My idea is use the analog input on esp32 to control engine sound, the horn controlled by digital input pin. Could you please give me advice how to get those relative code module from whole project
thank you alot for all your great work and kindly sharing!!!

Best regard!

rengels, 2024-02-26:
Thanks for the praise,

The SW isn't really that modular.
If you are fit in programming, you can replace the pwm input functions by something else.

An other solution would be to convert your 0-5v signal and the horn switch to PWM signals via an external (small) arduino.
Here is something that I found:
https://forum.arduino.cc/t/creating-your-own-pwm-to-control-a-servo/129869

Good luck

vinhx, 2024-02-27:
oh, I got your point!
I will try to replace the PWM signal by data mapping from analog input, thank you alot!

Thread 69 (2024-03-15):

ESP32 Blue Light Blinking !!Help Please!!

RS33D, 2024-03-15:
Hello

Your ESP32 engine sound project is very nice, currently trying to put it into my 3d printed 1/14 scale kenworth

But i have an issue with the circuit board not working, please see the below google drive video

[https://drive.google.com/file/d/1ZZUraMMt_CvwXIOm6ZMI8HmvmG5yAJjD/view?usp=sharing](url)

I have not adjusted the code as i want to use Sbus so just loaded the code up, but as per the video you can see that when turned on the blue light just flashes

i have adjusted the settings on the remote i am using which is a Flysky FS i6x and has its serial output set on S Bus, the receiver is also s bus compatible, i am using a flysky ia10b s receiver

i have also tried ibus, PWM and PPM and all result in the same issue

What have i done wrong??

your help would be much appreciated

many thanks

Lawson

FBester1976, 2024-03-15:
Good morning,

Some questions…

What does the serial monitor say? Keep your ESP32 plugged into the PC when you start it…serial monitor will state errors.
***@***.***
What version of software are you using?
Do you have the battery protection activated (3_ESC tab)?
***@***.***

I can see from your video that your ESC is plugged into the wrong position (not Ch1, needs to go to ESC.)
***@***.*** ***@***.***

Also plug in a speaker when you make the next video please.

Regards,

Frikkie

INTERNAL

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

RS33D, 2024-03-15:
Okay, thanks for your reply

Here is what the serial monitor says

**************************************************************************************************
TheDIYGuy999 RC engine sound & light controller for ESP32 software version 9.12.0
https://github.com/TheDIYGuy999/Rc_Engine_Sound_ESP32
Please read carefully: https://github.com/TheDIYGuy999/Rc_Engine_Sound_ESP32/blob/master/README.md
XTAL Frequency: 40 MHz, CPU Clock: 240 MHz, APB Bus Clock: 80000000 Hz
Internal RAM size: 289660 Byte, Free: 264244 Byte
WiFi MAC address: E4:65:B8:83:E7:48
Core 0 reset reason: 12: SW_CPU_RESET
Core 1 reset reason: 12: SW_CPU_RESET
**************************************************************************************************

EEPROM read.
current eeprom_id: 2
change it for default value upload!

Warning, BATTERY_PROTECTION disabled! ESC with low discharge protection required!
-------------------------------------
ENABLE_WIRELESS option enabled

Informations for web configuration via your cell phone or computer *******************************
SSID: My_Truck
Password: 123456789
IP address: 192.168.4.1

WiFi Tx Power Level: 78
WiFi Tx Power Level changed to: 28

The following trailers are currently enabled:
Trailer 1 MAC address: FE:49:01:00:00:01
-------------------------------------

**************************************************************************************************

Regarding the software i am using

Ardunio IDE is 1.8.15
Diyguy999 code version i am using is 9.12.0

No, i have not removed the \\ from battery protection, so I am assuming it is not activated

Please see the below video for when battery protection is enabled (ie \\ removed)

[https://drive.google.com/file/d/1QNNL5fuSMhIF74WCbjhMlbAaCGyKIKRQ/view?usp=sharing](url)

When battery protection is enabled, serial monitor will say this once, even if i am running it off my 2s lipo battery and just have the usb cord plugged into my computer

**************************************************************************************************
TheDIYGuy999 RC engine sound & light controller for ESP32 software version 9.12.0
https://github.com/TheDIYGuy999/Rc_Engine_Sound_ESP32
Please read carefully: https://github.com/TheDIYGuy999/Rc_Engine_Sound_ESP32/blob/master/README.md
XTAL Frequency: 40 MHz, CPU Clock: 240 MHz, APB Bus Clock: 80000000 Hz
Internal RAM size: 289272 Byte, Free: 263856 Byte
WiFi MAC address: E4:65:B8:83:E7:48
Core 0 reset reason: 1: POWERON_RESET
Core 1 reset reason: 14: EXT_CPU_RESET
Battery protection calibration data:
RESISTOR_TO_BATTTERY_PLUS: 10000 Ω
RESISTOR_TO_GND: 1000 Ω
DIODE_DROP: 0.00 V
**************************************************************************************************

EEPROM read.
current eeprom_id: 2
change it for default value upload!

Battery voltage: 1.58 V
Cutoff voltage per cell: 3.30 V
Fully charged voltage per cell: 4.20 V
Error, no valid battery detected! Only 2S & 3S batteries are supported!
REMOVE BATTERY, CONTROLLER IS LOCKED = 2 FAST FLASHES!

thanks for your comments so far.

FBester1976, 2024-03-16:
Good morning,

If you have not fitted the battery protection resistors on the back of the card, keep the // in place.

I also noticed that you have not powered the card through a y-lead from your battery.

[cid:25BAFFE4-087B-4324-B895-A9AD3ACF2061]

[cid:79CB54DC-D45A-427A-A690-8C273FBEAAEE]

I also do not see a speaker connected for the sound.

Regards,

Frikkie

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

RS33D, 2024-03-16:
Okay, should I be taking power from the battery to the esc as well as the
screw terminals on the circuit board?, is that what you mean by powering
through a y lead from the battery

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

FBester1976, 2024-03-16:
That is correct

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

RS33D, 2024-03-16:
Okay, please see the Google drive video, have just used jumper leads to
take power to circuit board, have also plugged in a speaker, which makes a
noise like a cricket when turned on

https://drive.google.com/file/d/1ZwvYzqQYg46y0y7oNw9ggOLlnbyNeDA-/view?usp=drivesdk

Many thanks

Lawson

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

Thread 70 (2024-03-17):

[Solved] Brownout detector was triggered

bereldhuin, 2024-03-17:
Hi,

I'm currently testing the sound module on a breadboard (sound + headlight and tail light only).

Everything is working fine until I raise the volume, at a not so high level.
At this time, the ESP32 reboots with a message "Brownout detector was triggered".

After looking for solutions on Internet, I tried using a better power supply (a Raspberry official 3A one) directly on 5V pin, or using a 47uF capacitor between GND and 3.3V, I didn't manage to solve this problem.

Do you have any idea ?
I saw that using a bredboard with PAM8403 is not ideal. Will a real PCB solve this issue ?

rengels, 2024-03-17:
The power regulators might not be fast enough if there is a sudden loud sound.
You might want to use different ones for the ESP and the audio amplifier, so that at least the esp32 supply is stable.

An oscilloscope might help in checking the voltages. There you can also see if your amplifier is creating noise on the power supply side.

I don't think that a PCB will solve the issue unless your cables are too thin or you'r routed your cables in an extremely bad way. It might be a loudspeaker with a too low resistance.

bereldhuin, 2024-03-17:
Thanks for your answer Ralph.

I'm using standard 4ohms, 5W speakers :
https://www.amazon.fr/dp/B08RY2VHZG?psc=1&ref=ppx_yo2ov_dt_b_product_details

From what I understood (and re-reading the scheamtics), I should use a MP1584 for AMP, and the BEC power for ESP32, right ?

rengels, 2024-03-18:
The AMP and voltage converter is pretty flexible. If you have a 5V battery, you might get away without any regulator.
Same for the AMP. If you want to use 12v for audio you can pick something else.

But the core of your issue seems to be that the voltage drops.
You should check that the VCC is stable enough.

bereldhuin, 2024-03-19:
I separated the power supply of the ESP32 (powered by microusb) and the AMP (powered by an external usb adapter) and everything is working fine now.

Even the interferences I got when the transmitter and receiver were on are gone. :-)

Thanks again for your help.

Closed 2024-03-19.

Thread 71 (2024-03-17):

Microprocessor Minimum Requirements

sk8board, 2024-03-17:
I noticed the documentation for this project does not list a minimum requirement for the micro. Would you know the minimum processor speed, RAM, ROM, and flash size for this project?

For example, will any version of ESP8266 or ESP32 or Pi Pico work?

https://www.espboards.dev/blog/esp32-soc-options/#esp32-versions-comparison

https://www.waveshare.com/wiki/RP2040-Zero#Specification

rengels, 2024-03-18:
The SW uses the dual core of the ESP32 and both cores are fairly maxed out.
Regarding the Flash I think we are at 60% usage.
The only viable option without many SW changes might be ESP32S3.

The SW isn't optimized at all, so you might be able to change it. But would need to invest a lot of time.

If I were you, I would just just the same HW that everyone else uses.

rengels, 2024-03-19:
I understand your problem now.

While playing audio does not need a lot of processing power, the Rc_Engine project does a lot of computation and mixing of sounds.
That pretty much uses up the 200MHz core at higher RPMs (the interrupt get's triggered more often at higher RPMs).

I am sure you can create a small, stripped down version of an engine sound generator on a much smaller CPU.
You would need a digital-to-analog converter though.

The Raspberry is powerfull enough for this, there is however one big downside.
You will need to implement this yourself.

So this discussion is pretty much theoretical, unless you manage to set up a project on your own. The code of the Rc_Engine_Sound project is not portable at all.

sk8board, 2024-03-19:
Thank you for your response.

Based on your input, I decided to look for the smallest ESP32 and found the [TinyPico Nano](https://www.tinypico.com/tinypico-nano) has the same specs as the ESP32-WROOM that you used. I designed a preliminary PCB to determine package size which includes an Express LRS (ELRS) receiver, 3A DC-DC power supply, Brushed ESC, and LED driver (58x38mm). The audio amplifier would need to be a separate board due to limited space on smaller WPL models. Changing to surface mound components would reduce size even more.

https://oshwlab.com/sk8board/esp32-elrs-receiver

I am looking at my options and would like to understand the challenges of adding Express LRS (ELRS) to your project. I was surprised to see some of your code is specific to FlySky transmitters. Is your code deeply connected to a FlySky transmitter? Would it be painfully difficult to add an ELRS transmitter and receiver to your code?

rengels, 2024-03-19:
Hi,
great that you found a nice HW.
The code is not specific to any transmitter. You can add your own stuff.

However, let me just repeat a part of my last message:

> So this discussion is pretty much theoretical, unless you manage to set up a project on your own. The code of the Rc_Engine_Sound project is not portable at all.

You would need someone with good experience in C and embedded programming.
I would also estimate the necessary time to port the code to another architecture and rip out the unnecessary parts at 80 hours.

It's probably easier to start from scratch and just copy the audio conversion tools and some of the samples.

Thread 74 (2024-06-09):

Through Hole Vs SMD

SteveGoral, 2024-06-09:
Good Afternoon,

Looking at PCBway, getting one of these boards assembled isnt very cost effective.  It's comes out at $88, and there are still components to source even after they have mounted the SMD parts.  Is there any chance of you releasing the files for the Through Hole board so I can get tat produced and then solder the whole thing myself?

TheDIYGuy999, 2024-06-09:
See hardware folder

SteveGoral, 2024-06-09:
Amazing thanks for the reply.  Is the functionality the same?  I've just retried a quote on PCBway and got a much more wallet friendly price, so just mulling it over.

fiechr, 2024-06-11:
As far as I remember, I got all the parts from AliExpress for maybe 20-30 EUR and 5-10 empty PCBs for less then 10 EUR. Don't pin me down on the exact prices, but it was definitely a lot less than $88 for multiple fully built controller boards.

I can't imagine through hole to be more cost effective, neither for production nor for sourcing parts (apart from parts that are through hole only, of course). If you don't mind soldering, I would always recommend to do it yourself.

I also recommend using the PCB with the switch mode voltage regulator module.

For more help you may want to check out this forum's thread (maybe you already did):
https://www.rc-modellbau-portal.de/index.php?threads/esp32-arduino-rc-sound-und-licht-controller.7183/

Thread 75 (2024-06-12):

esp32 i2s

yuranikspb, 2024-06-12:
I think it would be a good idea to switch from the internal dac to i2s, this will improve the sound quality and remove noise on the internal dac

rengels, 2024-06-14:
For sure this is a nice option.
I also would like to have outputs for LED via i2c so that more lights can be controlled.

However the project is quite often used in fairly small vehicles. Do you have a proposal for a small digital i2s amplifier board?

rambrosteam, 2024-09-18:
I have used MAX98357, The sound quality is crystal clear.
It is also available in breakout board form factor.

I tested it on a custom ESP32-S3 board.

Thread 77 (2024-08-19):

v9.12 error: 'timerAlarmWrite' was not declared in this scope;

Bananasmoothie1975, 2024-08-19:
On compiling v9.12 (actually now all versions I've tried), error of:

> error: 'timerAlarmWrite' was not declared in this scope; did you mean 'timerWrite'?

for all instances of 'timerAlarmwrite'.

Using IDE v2.3.2, ESP32Devkit1 board.
Have also had some issues with not finding folders, particularly "soc" folder which i can't find anywhere using File Explorer either.  EDIT:  Found the "soc" folder on an old drive from previous work.
Thanks

Bananasmoothie1975, 2024-08-21:
Looks like it's something to do with this (scroll to the Timer section):

https://docs.espressif.com/projects/arduino-esp32/en/latest/migration_guides/2.x_to_3.0.html#compilation-flags

Do I have to replace ALL the different API's or is there some sort of code auto update function?

TheDIYGuy999, 2024-08-21:
Use VS Code with PlatformIO instead of Arduino

Bananasmoothie1975, 2024-08-21:
> Use VS Code with PlatformIO instead of Arduino

Firstly, thanks for you reply and for all the effort in your RC controller, I have enjoyed all the videos and years ago built a PWM version for my HG P407 RC (modded to suit my own requirements) :D

I've now worked my way to a compileable sketch, I had to install the previous Espressif ESP32 API (v2.xxxx, down from v3.03) so the timer functions etc were correct.

I did download the VS Code software, but I have no idea what it does or how to use it :s

I'm now at the point of trying to get the SBUS working through my Flysky i6X and iA10B Rx, the serial monitor isn't showing any channel info, just EEPROM and core reg dump stuff but none of the individual channel stuff even shows up (none of the channel serialprint info).
SBUS to pin36 ("VP") if that helps.

FYI, I'm trained in mechanical systems, not electronics/code, but learning ;)

TheDIYGuy999, 2024-08-21:
This means it's compiling but crashing anyway. You need to use the correct, even older Espressif API. You should watch some VS Code tutorials and you will see it's way easier than Arduino, because it's installing all the correct API's and libraries automatically for you.

Bananasmoothie1975, 2024-10-15:
Eventually got VSCode and platformio etc working, code now compiles and uploads, thanks.

Closed 2024-10-15.

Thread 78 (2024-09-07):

problem with L120 profile

mroversi, 2024-09-07:
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

Hi,  is the code that is not working or I'm doing some errors?
I also made a new try with different  .ini
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

Would be nice to have the profile on the web app too
thanks

rengels, 2024-09-08:
Hi,
nice screenshots.

It would be better to push your changes, or at least post the diff here (instead of a screenshot).
From the error message I think that something with your environment is not OK.

Did you build prior to making the changes? As a baseline?

mroversi, 2024-09-09:
I just uploaded it ad didn't made any changes , just to upload the sw on the esp32.

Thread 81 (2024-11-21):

shaker only work with ps2 gamepad motor

Peyutron, 2024-11-21:
Hi!! Very good and excellent work. I have a slightly strange problem with the shaker. I have used a motor from a PS2 controller and it works very well. The problem is that if I try to connect a different type of motor like the one used by the smoke generator blower (just the motor) it doesn't do anything...
Also if I try a different type of engine. I have tested the breadboard with a transistor of the same type and both work, both the one I have for the shaker and the one for the blower.
I only have to ask if when defining the object shakerMotor.begin(SHAKER_MOTOR_PIN, 13, 20000); // Timer 13, 20kHz

Can the frequency make these motors not work?
I have tried different values   like 0, 100, 1000, 10000 and 50000.

Has this happened to anyone too?

Greetings!!!

TheDIYGuy999, 2024-11-22:
Thanks, adjust it here:
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

Peyutron, 2024-11-24:
Hi! Yes, I set all those values   to 255. Even so, the blower didn't work.
The problem was the resistor with the transistor (I'm using a BC547) which was 1K, I changed it to 330 and it works!!!

Now I can adjust the values.

Thank you very much and great job!!

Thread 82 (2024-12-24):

Hello everyone. i am having issues with upload the code of the older version 6.4. i have limited knowledge in coding and request someone to help me out please it will mean alot

Ritz-888, 2024-12-24:

TheDIYGuy999, 2024-12-24:
Why using an older version? If you have limited knowledge, you should try this first: https://thediyguy999.github.io/TheDIYGuy999_ESP32_Web_Flasher/flash.html

Ritz-888, 2024-12-24:
> Why using an older version? If you have limited knowledge, you should try this first: https://thediyguy999.github.io/TheDIYGuy999_ESP32_Web_Flasher/flash.html

im using the older version since i only want the sound and lights system not the dashboard. i have made my own rc trailer truck and its interior is not that good so iv decided not to have the displays

TheDIYGuy999, 2024-12-24:
You can use the current version, even if you don't have the dashboard. Just disable it.

Ritz-888, 2024-12-24:
> You can use the current version, even if you don't have the dashboard. Just disable it.
i tried the new version but i am finding it complicated. i am in year 11 and have very little knowledge about codding. i will really appreciate if you can help me step by step.

Ritz-888, 2024-12-24:
> You can use the current version, even if you don't have the dashboard. Just disable it.

i tried the new version but i am finding it challenging. i am in year 11 and have very little knowledge in codding. so if possible can you help me step by stem so i could complete my truck. i will be so thankful for your assistance.

TheDIYGuy999, 2024-12-24:
Have a look here: https://github.com/TheDIYGuy999/Rc_Engine_Sound_ESP32

here: https://www.facebook.com/groups/969278734997783

and here: https://www.rc-modellbau-portal.de/index.php?threads/esp32-arduino-rc-sound-und-licht-controller.7183/

Ritz-888, 2024-12-24:
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
How can i solve this errors

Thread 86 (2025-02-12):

please help  CH1: signal out of auto calibration range, check transmitter & receiver!

xskrtzx, 2025-02-12:
Hi There

I ran into a lot of dead ends because of my abilities.

First they said the battery voltage was low, where I had installed the regulator according to the schematic and components required. then I turned off the battery protection system,

it continues with
 **CH1: signal out of auto calibration range, check transmitter & receiver!**
what should I set? I didn't change anything programmed, sorry I'm new to RC and the ins and outs of it.

I use **RC RGT EX86190**
which uses the **dumborc X8e-150 gs07 remote**
and **X6DC receivers**. I just connected the **esp32** to the **sound amp**, then the **receiver** and **regulator**, all complete with the necessary **resistors** but the gas pedal didn't respond soundly when pressed

which parts do I need to setup in the program? I just want to get the sound out. sometimes the speaker just makes noise, I use **pam8403**

I hope you can help, I really appreciate it.

FBester1976, 2025-02-12:
Hello,

Which version of the code are you using?

I assume you are using PWM? I have seen on the forum that you must use code version 9.11.0 or older, on the newer versions the PWM does not work. I have not tested this, but people that struggled used the older code version and came right.

[https://www.rc-modellbau-portal.de/index.php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](url)
[https://www.rc-modellbau-portal.de/index.php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](url)

On the 2_Remote.h you must also make sure you select the correct remote, and have the SBUs and IBUS commented out (insert // before code)

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

You must also have a cable between your receiver and sound card for the 3 channels defined in the code. Please take note of the receiver channel and where the cable must go on the sound card.

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

Also not sure if you want to use the gearbox? Then you need to adjust the code to tell the SW which receiver channel will give the signal. I think on the DumboRC Ch4 is a 3 position switch.

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.

I hope this helps...

Regards,

Frikkie

xskrtzx, 2025-02-13:
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

I am not sure you can see clearly. Because they are still on breadboard. I also make my own diy soldering board but still process. I will finish it after this whole tested correctly.

I also supply my self with spare Ic, capacitor, resistor and esp32. Just for compare and try and error. So far I got one esp32 breakdown (it won't able to upload.

Well here the picture, thankyou for you time and effort for helping me out
Basically my wiring diagram is same as diyguy999 tutorial. But if you say pam8403 can operate 2.5-5v so now what the problem. With the same wiring way
- when I use my rc batteries to regulator (sound won't came out
- but when I use USB C direct to esp32 is connect. Maybe trouble in esp32 VIN?
-

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

FBester1976, 2025-02-13:
It is impossible for me to check the breadboard connections.

Please note there is 2 different 5V inputs, one from the ESC that is connected to the headers, and one from the 5V regulator.

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

So with the printed PCB I know it is important to either have the ESC plugged into the headers to supply 5V, or have a jumper in place.

Did you change the code in the Remote tab to have None for Ch3. I see no wire from the RX to your breadboard. Not sure if it will work correctly if it gets no signal for Ch3.

Not sure where in the world you are, but ordering the PCB's from PCBWay to South Africa was not that expensive, and makes live a lot easier!

xskrtzx, 2025-02-28:
> It is impossible for me to check the breadboard connections.

Hi,

Finally I can finished this stuff after So much drama. Lol

So I continued with my DIY PCB. I'm just lazy to sit still and wait for the pcb order. All the components are complete so why wait. On your advice I use pwm. And version 9.11 For rc RGT ex86190. But I just confused how to activated horn. I just try all my button and set in the remote adjustment but still not working

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

Closed 2025-03-02.

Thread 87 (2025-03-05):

Errors when Compiling Code 9.1.3 with Arduino IDE 2.3.4

JPS952, 2025-03-05:
I'm trying to compile for my tank using the IS3.h  as vehicle choice. ESP32 is the "DOIT ESP32 DEVKIT V1"
but am getting this error.

=====================
C:\_Arduino\Rc_Engine_Sound_ESP32-9.13\Rc_Engine_Sound_ESP32\src\src.ino:99:10: fatal error: soc/rtc_wdt.h: No such file or directory
   99 | #include "soc/rtc_wdt.h"  // for watchdog timer
      |          ^~~~~~~~~~~~~~~
compilation terminated.
exit status 1

Compilation error: soc/rtc_wdt.h: No such file or directory
==========================

Please help.  The last time I successfully compiled was for version 5.8.
Thanks!

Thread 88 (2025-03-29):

Battery low discharge protection

skypeja, 2025-03-29:
In the code in Esc.h is part Battery low discharge protection, but there is no said which pin is used to read voltage from voltage divider. Can anyone help me, please?

skypeja, 2025-03-30:
Just found in src.ino --- #define BATTERY_DETECT_PIN **_39_** // Voltage divider resistors connected to pin "VN & GND"
my bad, sorry

Closed 2025-03-30.

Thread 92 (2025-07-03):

no sound

radu022003, 2025-07-03:
Hello,
my hardware at the moment looks like the prototype on the documentation page.
Instead of the RC receiver, I am using a servo tester.
I have commented out all communication protocols in order to use the classic PWM RC signals (i hope that this is the correct way).

I have connected the output of the servo tester through 330ohm resistors to pins D13 and D14.
I have sound output because I get the "fuel low voice message"

when the device starts I can hear 3 "clicks", but no sound anymore. I have no lights connected. My purpose is to use it on a RC boat.

the serial monitor is writing this:
```
**************************************************************************************************
TheDIYGuy999 RC engine sound & light controller for ESP32 software version 9.13.0
https://github.com/TheDIYGuy999/Rc_Engine_Sound_ESP32
Please read carefully: https://github.com/TheDIYGuy999/Rc_Engine_Sound_ESP32/blob/master/README.md
XTAL Frequency: 40 MHz, CPU Clock: 240 MHz, APB Bus Clock: 80000000 Hz
Internal RAM size: 382096 Byte, Free: 356096 Byte
WiFi MAC address: E8:6B:EA:D4:8F:E8
Core 0 reset reason: 1: POWERON_RESET
Core 1 reset reason: 14: EXT_CPU_RESET
**************************************************************************************************

EEPROM read.
current eeprom_id: 5
change it for default value upload!

Battery protection calibration data: ----
RESISTOR_TO_BATTTERY_PLUS: 9400 Ω
RESISTOR_TO_GND: 1000 Ω
DIODE_DROP: 0.31 V

ESC calibration data: ----
ESC pulse span: 600 (Used to adjust the top speed: 500 = full ESC power, 1000 = half ESC power etc.)
ESC takeoff punch: 0 (Usually 0. Enlarge it up to about 150, if your motor is too weak around neutral.)
ESC reverse plus: 0 (Usually 0. Enlarge it up to about 220, if your reverse speed is too slow.)
ESC ramp time for crawler mode: 10 (about 10 - 15), less = more direct control = less virtual inertia)
**************************************************************************************************

ENABLE_WIRELESS option disabled, no WiFi configuration or ESP-Now Trailer!
-------------------------------------
Battery voltage: 3.79 V
Cutoff voltage per cell: 3.30 V
Fully charged voltage per cell: 4.20 V
Number of cells: 3 (3S battery detected) Based on setpoint: 8.55 V
Battery cutoff voltage: 3.30 V (3 * 3.30 V)
-------------------------------------
... PWM communication mode active.
-------------------------------------
Standard ESC mode configured. Connect crawler ESC to ESC header. RZ7886 motor driver not usable!
-------------------------------------
```

TheDIYGuy999, 2025-07-03:
Change this:

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

radu022003, 2025-07-03:
Thank you for the fast response, I did the change accordingly, now the 3 clicks are gone, it is complete silence.

```
**************************************************************************************************
TheDIYGuy999 RC engine sound & light controller for ESP32 software version 9.13.0
https://github.com/TheDIYGuy999/Rc_Engine_Sound_ESP32
Please read carefully: https://github.com/TheDIYGuy999/Rc_Engine_Sound_ESP32/blob/master/README.md
XTAL Frequency: 40 MHz, CPU Clock: 240 MHz, APB Bus Clock: 80000000 Hz
Internal RAM size: 382844 Byte, Free: 356844 Byte
WiFi MAC address: E8:6B:EA:D4:8F:E8
Core 0 reset reason: 1: POWERON_RESET
Core 1 reset reason: 14: EXT_CPU_RESET
**************************************************************************************************

EEPROM read.
current eeprom_id: 5
change it for default value upload!

ESC calibration data: ----
ESC pulse span: 600 (Used to adjust the top speed: 500 = full ESC power, 1000 = half ESC power etc.)
ESC takeoff punch: 0 (Usually 0. Enlarge it up to about 150, if your motor is too weak around neutral.)
ESC reverse plus: 0 (Usually 0. Enlarge it up to about 220, if your reverse speed is too slow.)
ESC ramp time for crawler mode: 10 (about 10 - 15), less = more direct control = less virtual inertia)
**************************************************************************************************

ENABLE_WIRELESS option disabled, no WiFi configuration or ESP-Now Trailer!
-------------------------------------
Warning, BATTERY_PROTECTION disabled! ESC with low discharge protection required!
-------------------------------------
... PWM communication mode active.
-------------------------------------
Standard ESC mode configured. Connect crawler ESC to ESC header. RZ7886 motor driver not usable!
-------------------------------------

Transmitter channel offsets (calculated, if channelAutoZero[] = true):
 CH1: -25 µs
 CH3: -26 µs
 CH5: signal out of auto calibration range, check transmitter & receiver!
```

radu022003, 2025-07-04:
i have looked into the line 2187 of the file src.ino, by placing a serial.print there for the channel3. I could observe that the readings are made and the value changes with the potentiometer position, of the servotester. but the serial is printing only one time, at the beginning, then nothing more.

Closed 2025-07-18.

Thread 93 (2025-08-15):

Kids PowerWheels -mode?

Larsuu, 2025-08-15:
Hey

This is just my idea and project stub i'd like to share. If someone likes to copy, as it is really cool for kids.

I helped our local fire department museum to wire up 1:2 scale DIY firetrucks alarm sounds and lights. This is a kind of big powerwheels that volunteering firemen had built during the previous years from lawn mover and plywood. It was requested to have lights and i did them. Halfway through the project i found this project. (yes, i had been following diyguy99 for years, but just couldn't remember this. Maybe i'll add some video and pictures later on.)

I wasn't able to put lights & blinkers under rc_engine_sound system due to time shortage. But i added the throttle sound and it is really cool, specially with a big subwoofer its really something else. My 3yr old spent many days just testing the throttle sound with a steering wheel driving places in his imagination. A year later later i got this kids police powerwheels car for my youngest. And this project came again on my table. i would like to transform the current powerwheels to "street legal" version (not a public road though).

So, my idea is this:

- Local, Standalone version or 2nd ESP32 to read inputs of car control devices or something compatible.

The current setup is possibly a bit hard to make for novices when not having any RC remote controls. I used the RC_sound_system in PWM mode and set up a second ESP32 to read PC gaming pedals input with a ADC to PWM conversion. Would anyone know if there be a compatible options built in the code to do this without the 2nd ESP32 or does the RC hobby people know a "3v3 safe input multiplexer" in the RC field that would fit right in?

This is where my own future  project differs from possible simple switch throttle lead acid powerwheels configuration options:

(My future powerwheels mod -> hoverboard as wheels, analog throttle reading)
So lets say if throttle input would need a ADC reading and the rest could be just switches, so 1 ADC + digitalread/writes. Its not easy to fit it in the code, i know. So i would prefer just some external hardware to do this, so your project would have minimal if not any affect.

With original simpler powerwheels the throttle is just a switch, so maybe it could be just digitalRead inputs. (with my OCD, this isnt enough, i need real proportional control on the throttle for my kid. Maybe even flood lights and all the brake lights etc... i know i can do this with simple local wiring. ler powerwheels the throttle is just a switch, so maybe it could be just digitalRead inputs. (with my OCD, this isnt enough, i need real proportional control on the throttle for my kid. Maybe even flood lights and all the brake lights etc... i know i can do this with simple local wiring.

Is this even possible without big involment. i know that the time which i dont have, so i dont expect you to have it either. Kids don't require much, so maybe it all would go with some simple config text copy paste + #ifdef ? I'm not asking for new code. Kids aint OCD accurate on these things. But if i were to guess without reading the code, the local standalone version would have problems with reading one or multiple analog values from potentiometer. Would it be possible to have some sort of analog-to-PPM or -to-PWM PCB from aliexpress that is general & easy to understand for hobbyist?  So i could run it straight as is with PWM/PPM mode? I could make it in kicad and have the board just for me and if worthy of a include in your project it would get just increased complexity. I'm trying to have something done so it would require a engineer to have it done by someone else.

With fast googling, i found many voltage to PPM converter but those were with a 0-5V output. They are easy to make into 3V3 with voltage divider or with logic leve shifter, but that quickly turns things into a complicated wiring. Not a problem for me, but reduces the idea of scalability.

It could make for a cool youtube video as well. Imagine kids having monster truck sound and shakers and all, blinkers etc.. on a powerwheels. We also have this small kids car park, where you can practice driving with crossing lights and all. Maybe i'll have it ready for next summer.

ps. i had a pretty bad burnout, doctors even tried to label psychosis on me :D so i'm not really asking anything that i couldn't do myself. i know these systems pretty ok and i know c++ etc... But as some might know from experience,  i'm trying to protect myself but at the same time offer my kids something minimal i can maybe do. I'm better now. But i would be thankful for all the pointers to what to avoid and what cant be done. Maybe i'll even dig in to the code, but for now i'll go with just making a quick and dirty AI written ESP32 input translator as soon as they arrive.

Well.. thats for now. Messy text, sorry. A lot of interruptions.

Larsuu, 2025-08-17:
Indeed, that looks nice. Thank you.

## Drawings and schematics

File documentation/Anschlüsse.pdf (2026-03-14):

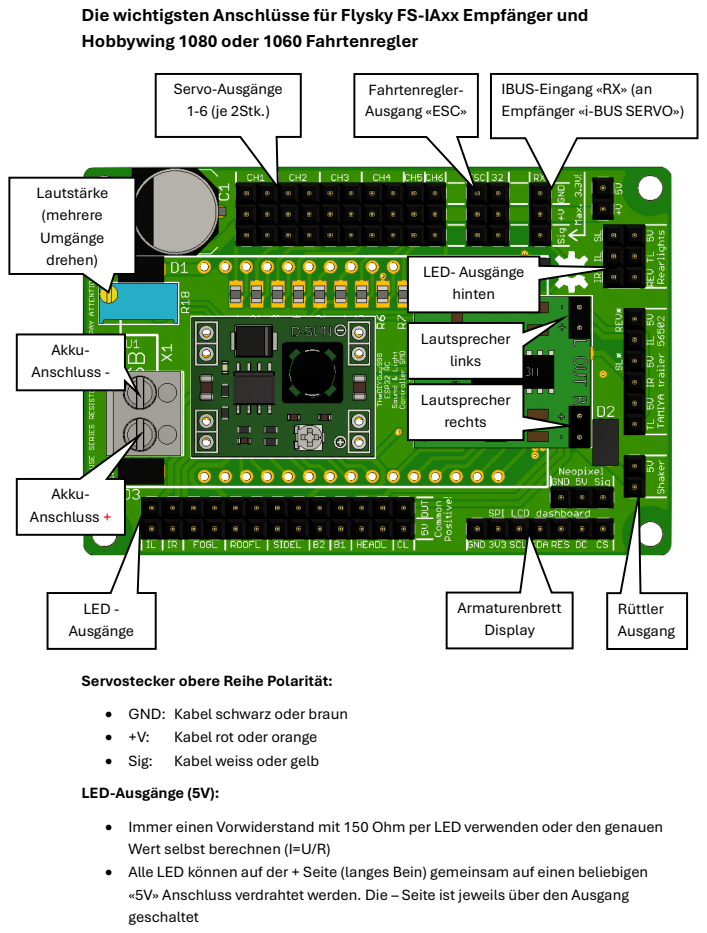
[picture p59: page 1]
Kabel rot oder orange; Servo-Ausgänge 1-6 (je 2Stk.); Fahrtenregler- Ausgang «ESC»; LED - Ausgänge; Armaturenbrett Display; Rüttler Ausgang; LED- Ausgänge hinten; Lautsprecher links; Lautsprecher rechts; Lautstärke (mehrere Umgänge drehen); Akku- Anschluss +; Akku- Anschluss -

Die wichtigsten Anschlüsse für Flysky FS-IAxx Empfänger und
Hobbywing 1080 oder 1060 Fahrtenregler

IBUS-Eingang «RX» (an
Empfänger «i-BUS SERVO»)

Servostecker obere Reihe Polarität:
• GND: Kabel schwarz oder braun
• Sig: Kabel weiss oder gelb
LED-Ausgänge (5V):
• Immer einen Vorwiderstand mit 150 Ohm per LED verwenden oder den genauen
Wert selbst berechnen (I=U/R)
• Alle LED können auf der + Seite (langes Bein) gemeinsam auf einen beliebigen
«5V» Anschluss verdrahtet werden. Die – Seite ist jeweils über den Ausgang
geschaltet

Bezeichnung der LED-Anschlüsse:

Beschriftung | English | Deutsch | Bemerkung
IL | Indicator Left | Blinker Links
IR | Indicator Right | Blinker Rechts
FOGL | Fog Lights | Nebellampen
ROOFL | Roof Lights | Dachleuchten
SIDEL (SL) | Side Lights | Seitenmarkierungsleuchten | Nicht mit Armaturenbrett
B1 | Beacon 1 | Blinklicht 1 | Nicht mit Armaturenbrett
B2 | Beacon 2 | Blinklicht 2 | Nicht mit Armaturenbrett
HEADL | Headlights | Abblendlicht & Fernlicht
CL | Cab Lights | Kabinen-Innenbeleuchtung
TL | Taillights | Schlusslicht & Bremslicht
REV | Reversing Lights | Rückfahrlicht

Weiteres:

- Der Rüttler ist ebenso wie gewisse Lichtanschlüsse nicht in Kombination mit einem aktivierten Armaturenbrett verwendbar
- Die weisse oder gelbe Signalader des IBUS-Kabels zum «RX»-Eingang muss am Flysky-Empfänger auf der Seite mit dem kleinen grünen Nocken der Beschriftung sein

Sender-Einstellungen Flysky FS-I6S:
1) = Dual Rate abhängig
Kanal | Zugewiesener Schalter | Funktion
1 | | Lenkung
2 | | Motorbremse, Licht, Lautstärke, Motor ein / aus 1)
3 | | Gas und Bremse
4 | | Blinker und Warnblinker 1)
6 | VRA | Horn & Sirene
7 | VRB | Kippen
| SWA | Dual Rate (oben = 100%, unten = 75%)
9 | SWB | -
10 | SWC | Getriebe 1. Bis 3. Gang (wenn nicht Automatik)

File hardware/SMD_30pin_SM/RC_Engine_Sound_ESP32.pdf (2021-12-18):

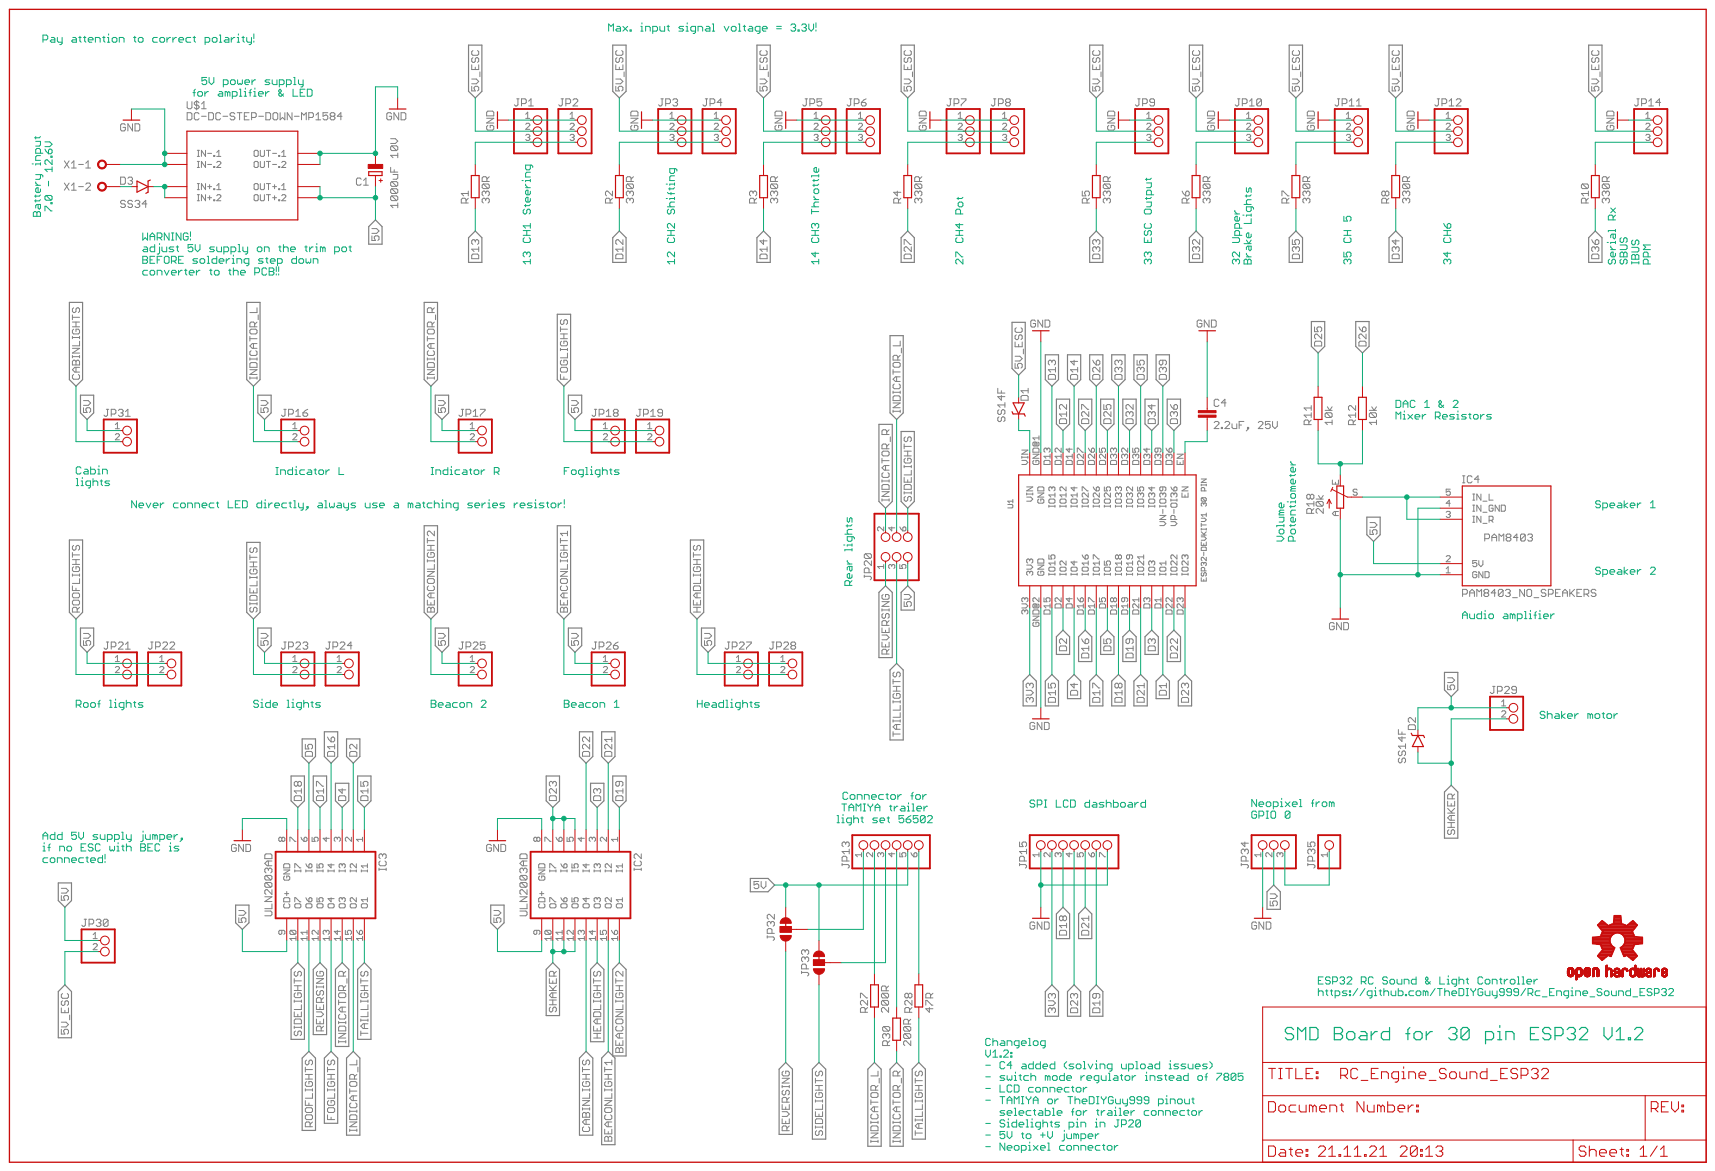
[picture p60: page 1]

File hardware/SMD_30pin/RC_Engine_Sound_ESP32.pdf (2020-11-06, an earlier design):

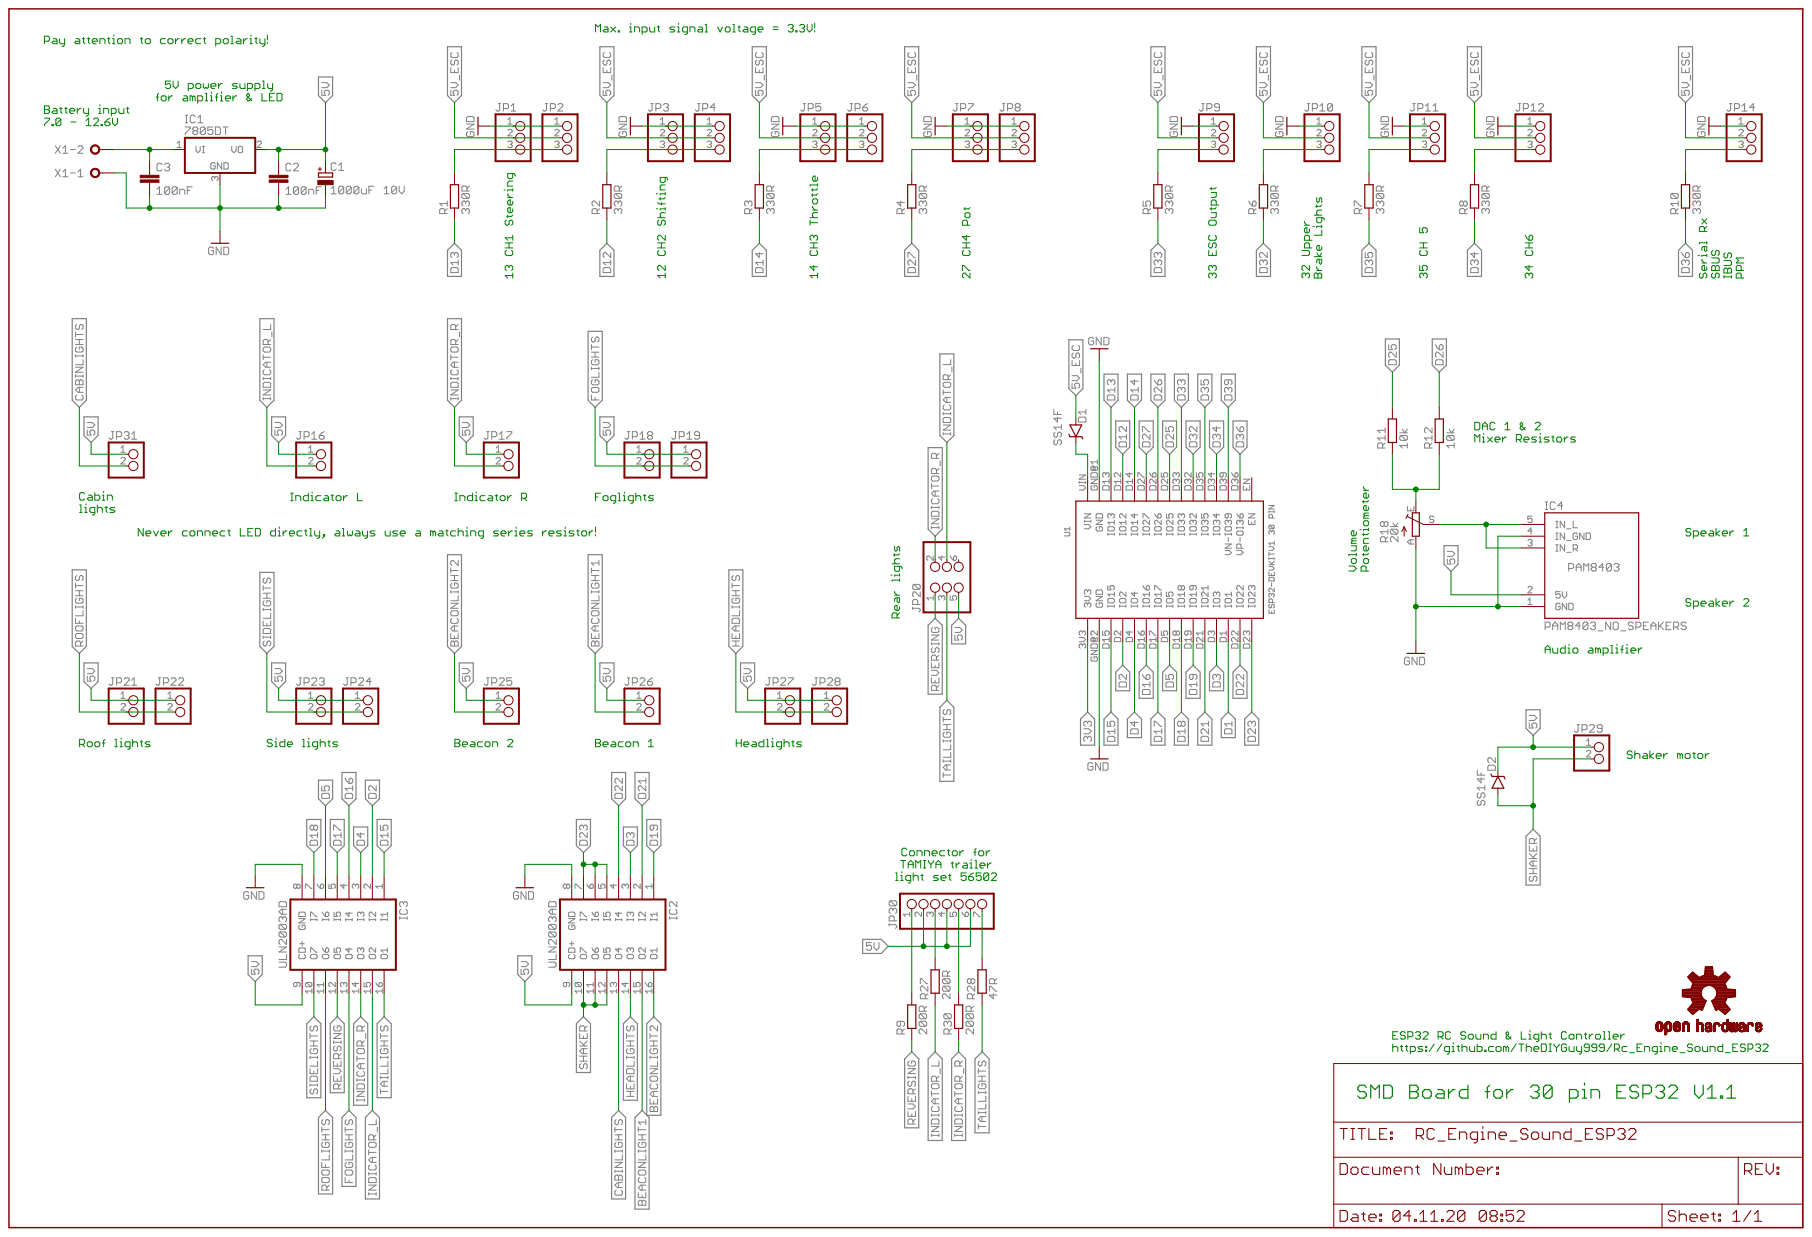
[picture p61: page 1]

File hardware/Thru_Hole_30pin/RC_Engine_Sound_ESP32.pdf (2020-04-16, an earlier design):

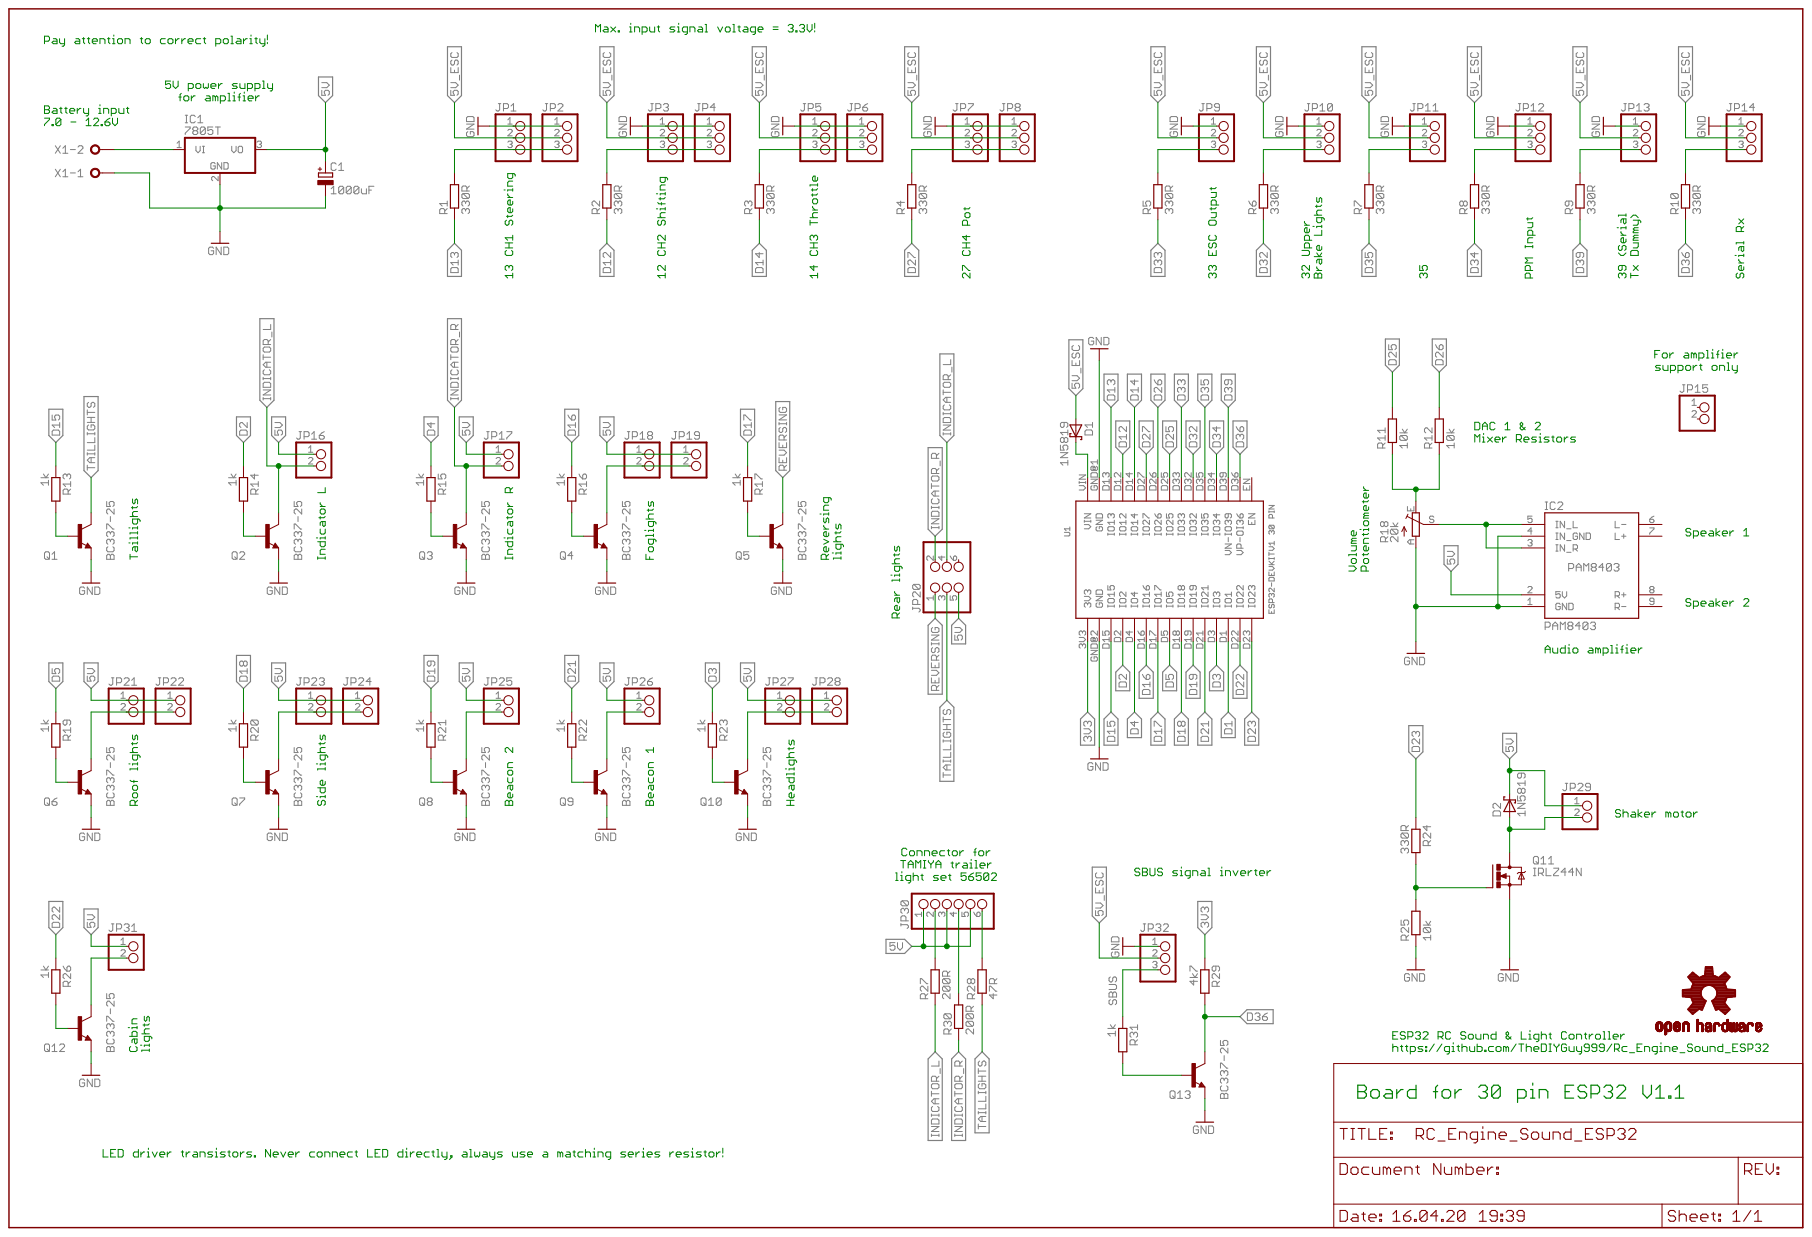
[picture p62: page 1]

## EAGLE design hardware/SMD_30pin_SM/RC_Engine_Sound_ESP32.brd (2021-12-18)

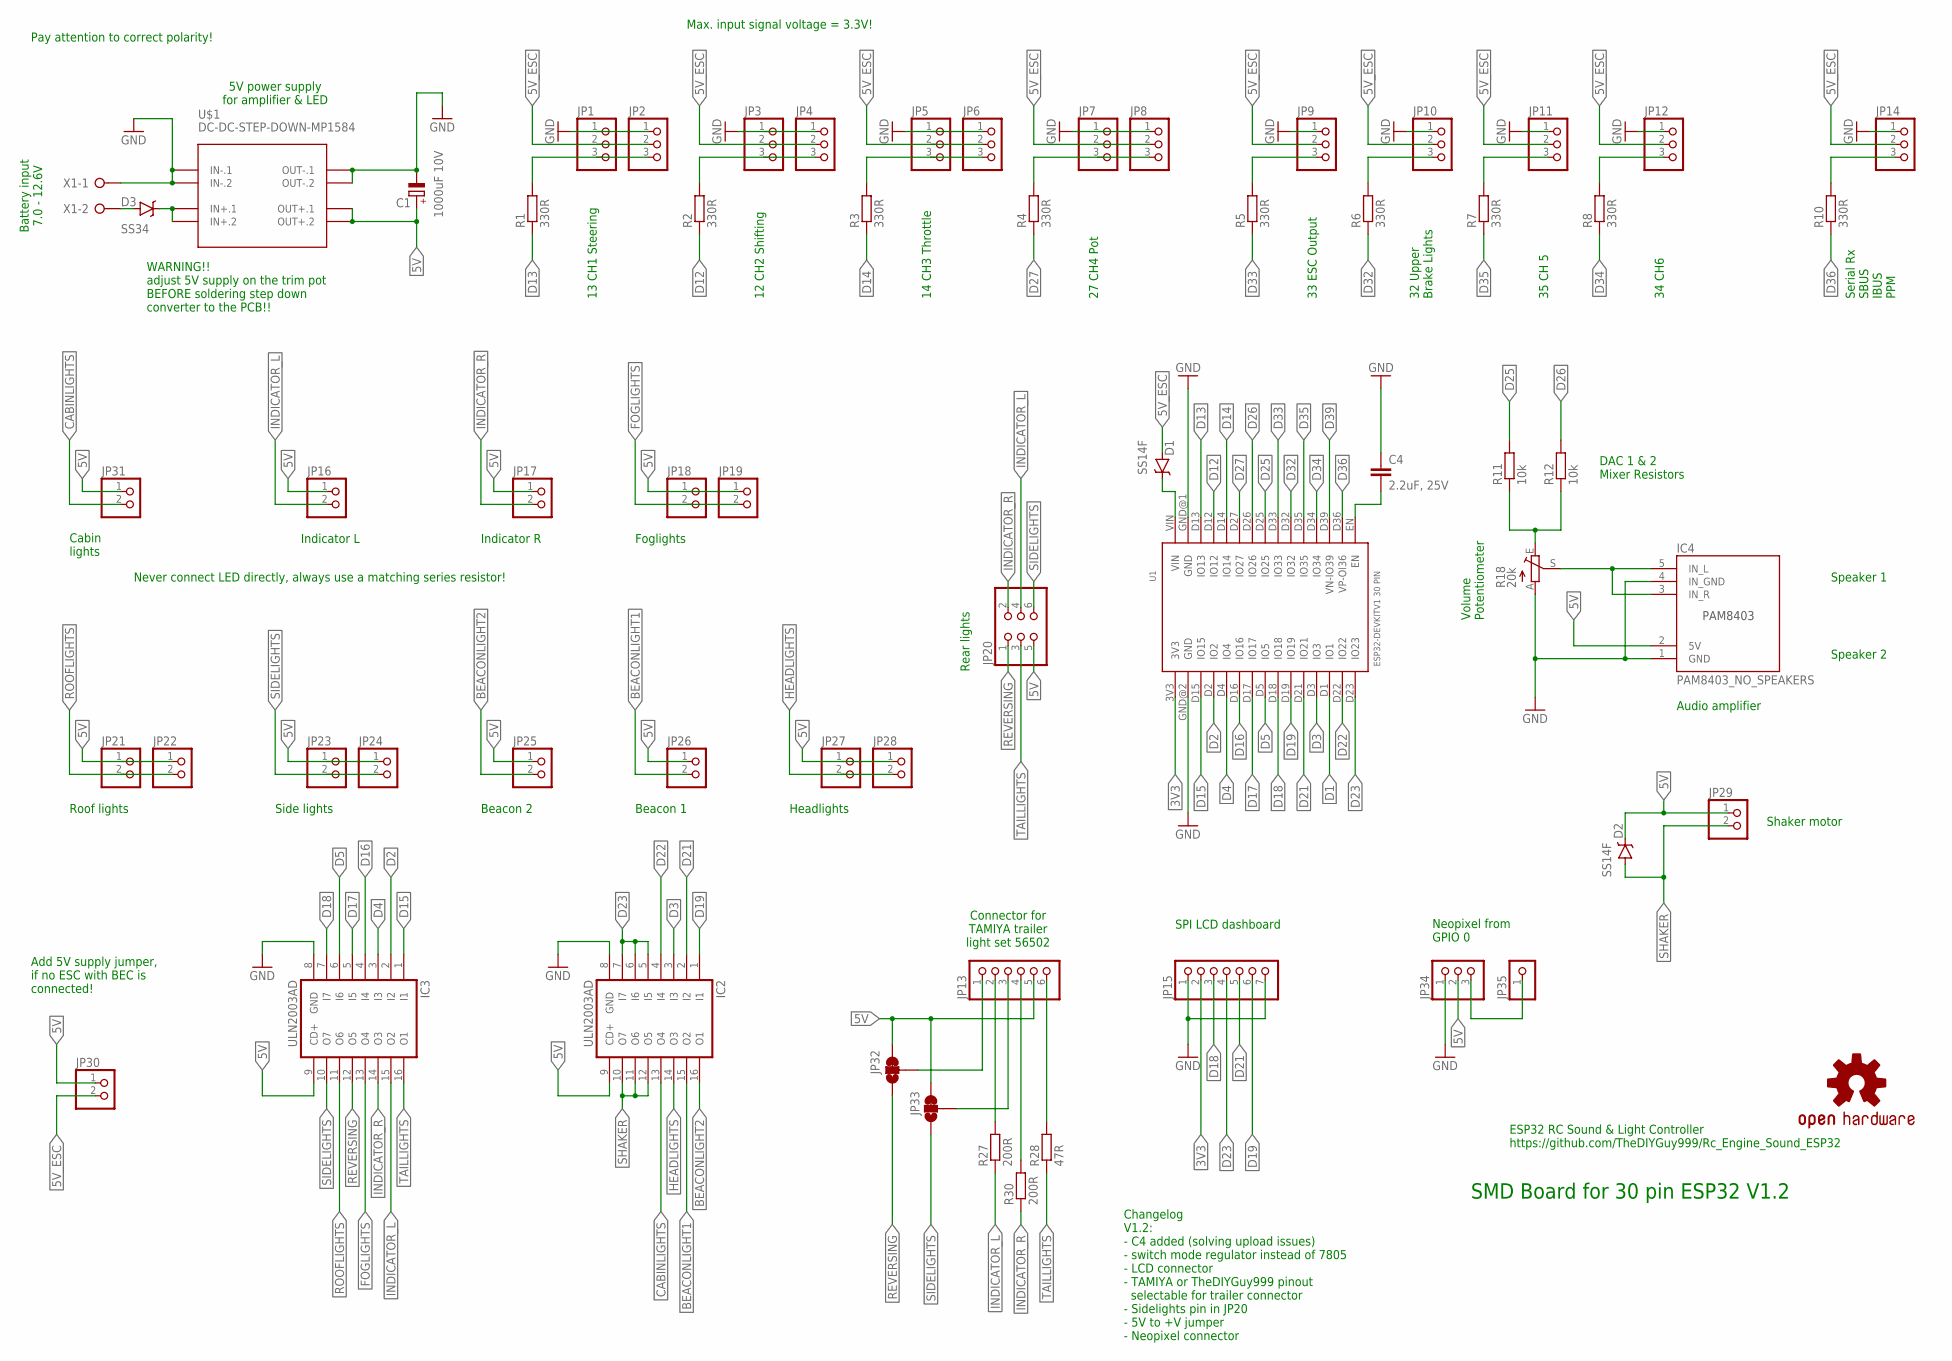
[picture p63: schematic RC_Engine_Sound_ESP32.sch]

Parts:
C1: 1000uF 10V; UD-10X10_NICHICON
C4: 2.2uF, 25V; C1206
D1, D2: SS14F; SMA-DIODE
D3: SS34; SMA-DIODE
IC2, IC3: ULN2003AD; SO16
IC4: PAM8403_NO_SPEAKERS
JP1, JP2, JP3, JP4, JP5, JP6, JP7, JP8, JP9, JP10, JP11, JP12, JP14, JP34: PINHD-1X3; 1X03
JP13: PINHD-1X6; 1X06
JP15: PINHD-1X7; 1X07
JP16, JP17, JP18, JP19, JP21, JP22, JP23, JP24, JP25, JP26, JP27, JP28, JP29, JP30, JP31: PINHD-1X2; 1X02
JP20: PINHD-2X3; 2X03
JP32, JP33: JUMPER-PAD-3-2OF3_NC_BY_TRACE_LARGE; PAD-JUMPER-3-2OF3_NC_BY_TRACE_YES_SILK_LARGE
JP35: PINHD-1X1; 1X01
LOGO1: OSHW-LOGOM; OSHW-LOGO-M
R1, R2, R3, R4, R5, R6, R7, R8, R10: 330R; R0805
R11, R12: 10k; R0805
R18: 20k; S64W
R27, R30: 200R; R0805
R28: 47R; R0805
U1: ESP32DEVKITV1; ESP32-DEVKITV1
U$1: DC-DC-STEP-DOWN-MP1584
X1: W237-02P; W237-132

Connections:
3V3: JP15.2, U1.3V3
5V: C1.+, D2.C, IC2.9 (CD+), IC3.9 (CD+), IC4.2 (5V), JP13.5, JP16.1, JP17.1, JP18.1, JP19.1, JP20.5, JP21.1, JP22.1, JP23.1, JP24.1, JP25.1, JP26.1, JP27.1, JP28.1, JP29.1, JP30.1, JP31.1, JP32.3, JP33.3, JP34.2, U$1.OUT+.1, U$1.OUT+.2
5V_ESC: D1.A, JP1.2, JP2.2, JP3.2, JP4.2, JP5.2, JP6.2, JP7.2, JP8.2, JP9.2, JP10.2, JP11.2, JP12.2, JP14.2, JP30.2
BEACONLIGHT1: IC2.15 (O2), JP26.2
BEACONLIGHT2: IC2.16 (O1), JP25.2
CABINLIGHTS: IC2.13 (O4), JP31.2
D0: JP34.3, JP35.1
D1: U1.D1 (IO1)
D2: IC3.2 (I2), U1.D2 (IO2)
D3: IC2.3 (I3), U1.D3 (IO3)
D4: IC3.3 (I3), U1.D4 (IO4)
D5: IC3.6 (I6), U1.D5 (IO5)
D12: R2.1, U1.D12 (IO12)
D13: R1.1, U1.D13 (IO13)
D14: R3.1, U1.D14 (IO14)
D15: IC3.1 (I1), U1.D15 (IO15)
D16: IC3.4 (I4), U1.D16 (IO16)
D17: IC3.5 (I5), U1.D17 (IO17)
D18: IC3.7 (I7), JP15.3, U1.D18 (IO18)
D19: IC2.1 (I1), JP15.6, U1.D19 (IO19)
D21: IC2.2 (I2), JP15.5, U1.D21 (IO21)
D22: IC2.4 (I4), U1.D22 (IO22)
D23: IC2.5 (I5), IC2.6 (I6), IC2.7 (I7), JP15.4, U1.D23 (IO23)
D25: R11.2, U1.D25 (IO25)
D26: R12.2, U1.D26 (IO26)
D27: R4.1, U1.D27 (IO27)
D32: R6.1, U1.D32 (IO32)
D33: R5.1, U1.D33 (IO33)
D34: R8.1, U1.D34 (IO34)
D35: R7.1, U1.D35 (IO35)
D36: R10.1, U1.D36 (VP-OI36)
D39: U1.D39 (VN-IO39)
FOGLIGHTS: IC3.13 (O4), JP18.2, JP19.2
GND: C1.-, C4.1, IC2.8 (GND), IC3.8 (GND), IC4.1 (GND), IC4.4 (IN_GND), JP1.1, JP2.1, JP3.1, JP4.1, JP5.1, JP6.1, JP7.1, JP8.1, JP9.1, JP10.1, JP11.1, JP12.1, JP14.1, JP15.1, JP15.7, JP34.1, R18.A, U1.GND@1 (GND), U1.GND@2 (GND), U$1.IN-.1, U$1.IN-.2, U$1.OUT-.1, U$1.OUT-.2, X1.1
HEADLIGHTS: IC2.14 (O3), JP27.2, JP28.2
INDICATOR_L: IC3.15 (O2), JP16.2, JP20.4, R27.1
INDICATOR_R: IC3.14 (O3), JP17.2, JP20.2, R30.1
unnamed: IC4.3 (IN_R), IC4.5 (IN_L), R18.S
unnamed: R11.1, R12.1, R18.E
unnamed: JP1.3, JP2.3, R1.2
unnamed: JP13.6, R28.2
unnamed: JP3.3, JP4.3, R2.2
unnamed: JP5.3, JP6.3, R3.2
unnamed: JP7.3, JP8.3, R4.2
unnamed: JP9.3, R5.2
unnamed: D1.C, U1.VIN
unnamed: JP10.3, R6.2
unnamed: JP11.3, R7.2
unnamed: JP12.3, R8.2
unnamed: JP13.4, R30.2
unnamed: JP14.3, R10.2
unnamed: JP13.2, R27.2
unnamed: JP13.1, JP32.2
unnamed: C4.2, U1.EN
unnamed: JP13.3, JP33.2
unnamed: D3.C, U$1.IN+.1, U$1.IN+.2
unnamed: D3.A, X1.2
REVERSING: IC3.12 (O5), JP20.1, JP32.1
ROOFLIGHTS: IC3.11 (O6), JP21.2, JP22.2
SHAKER: D2.A, IC2.10 (O7), IC2.11 (O6), IC2.12 (O5), JP29.2
SIDELIGHTS: IC3.10 (O7), JP20.6, JP23.2, JP24.2, JP33.1
TAILLIGHTS: IC3.16 (O1), JP20.3, R28.1

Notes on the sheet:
Speaker 1
Speaker 2
13 CH1 Steering
12 CH2 Shifting
14 CH3 Throttle
27 CH4 Pot
33 ESC Output
32 Upper Brake Lights
35 CH 5
34 CH6
Serial Rx SBUS IBUS PPM
DAC 1 & 2 Mixer Resistors
Audio amplifier
Volume Potentiometer
5V power supply for amplifier & LED
Battery input 7.0 - 12.6V
SMD Board for 30 pin ESP32 V1.2
Shaker motor
Headlights
Foglights
Indicator L
Indicator R
Roof lights
Side lights
Connector for TAMIYA trailer light set 56502
Rear lights
ESP32 RC Sound & Light Controller https://github.com/TheDIYGuy999/Rc_Engine_Sound_ESP32
Never connect LED directly, always use a matching series resistor!
Beacon 2
Beacon 1
Cabin lights
Pay attention to correct polarity!
Max. input signal voltage = 3.3V!
Changelog V1.2: - C4 added (solving upload issues) - switch mode regulator instead of 7805 - LCD connector - TAMIYA or TheDIYGuy999 pinout selectable for trailer connector - Sidelights pin in JP20 - 5V to +V jumper - Neopixel connector
WARNING!! adjust 5V supply on the trim pot BEFORE soldering step down converter to the PCB!!
SPI LCD dashboard
Add 5V supply jumper, if no ESC with BEC is connected!
Neopixel from GPIO 0

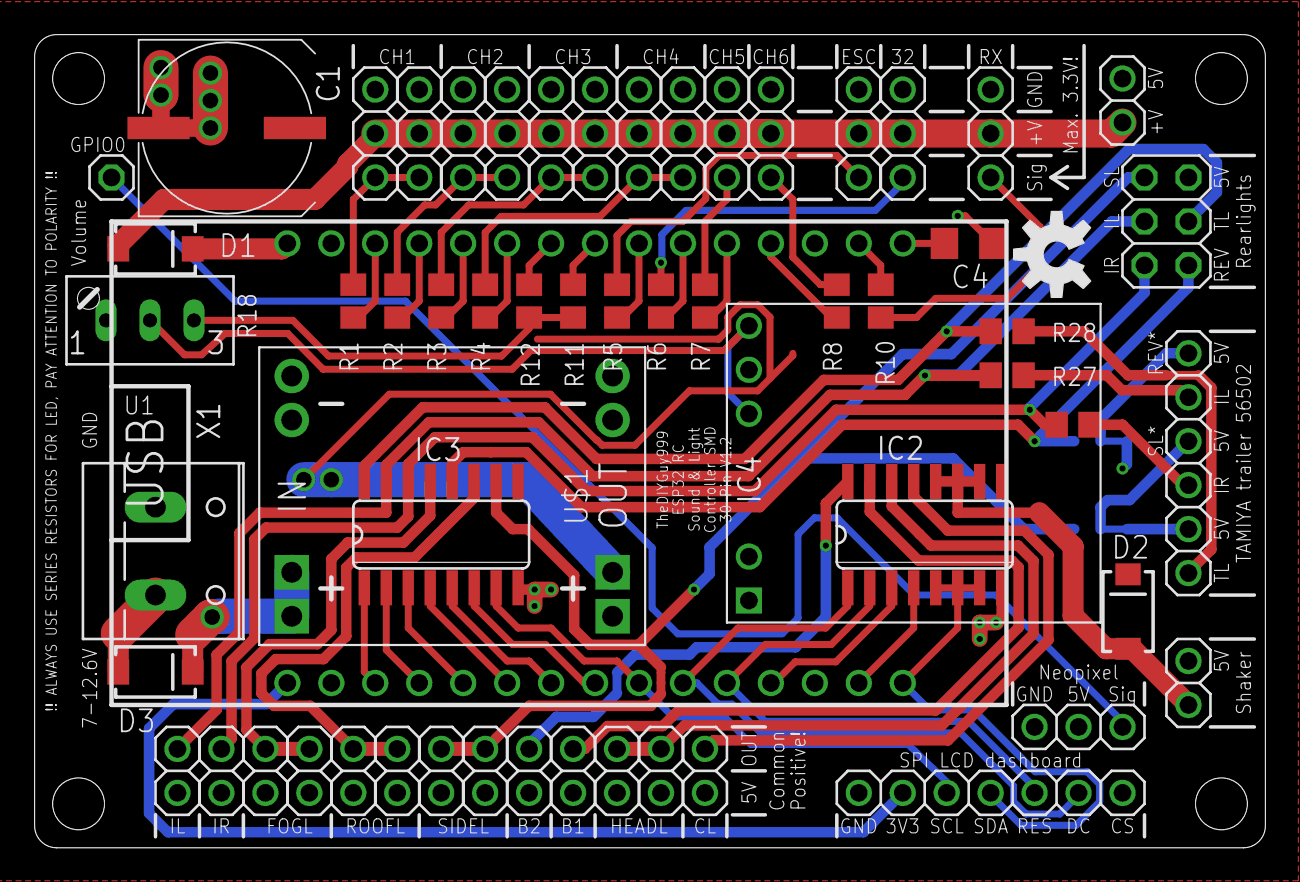
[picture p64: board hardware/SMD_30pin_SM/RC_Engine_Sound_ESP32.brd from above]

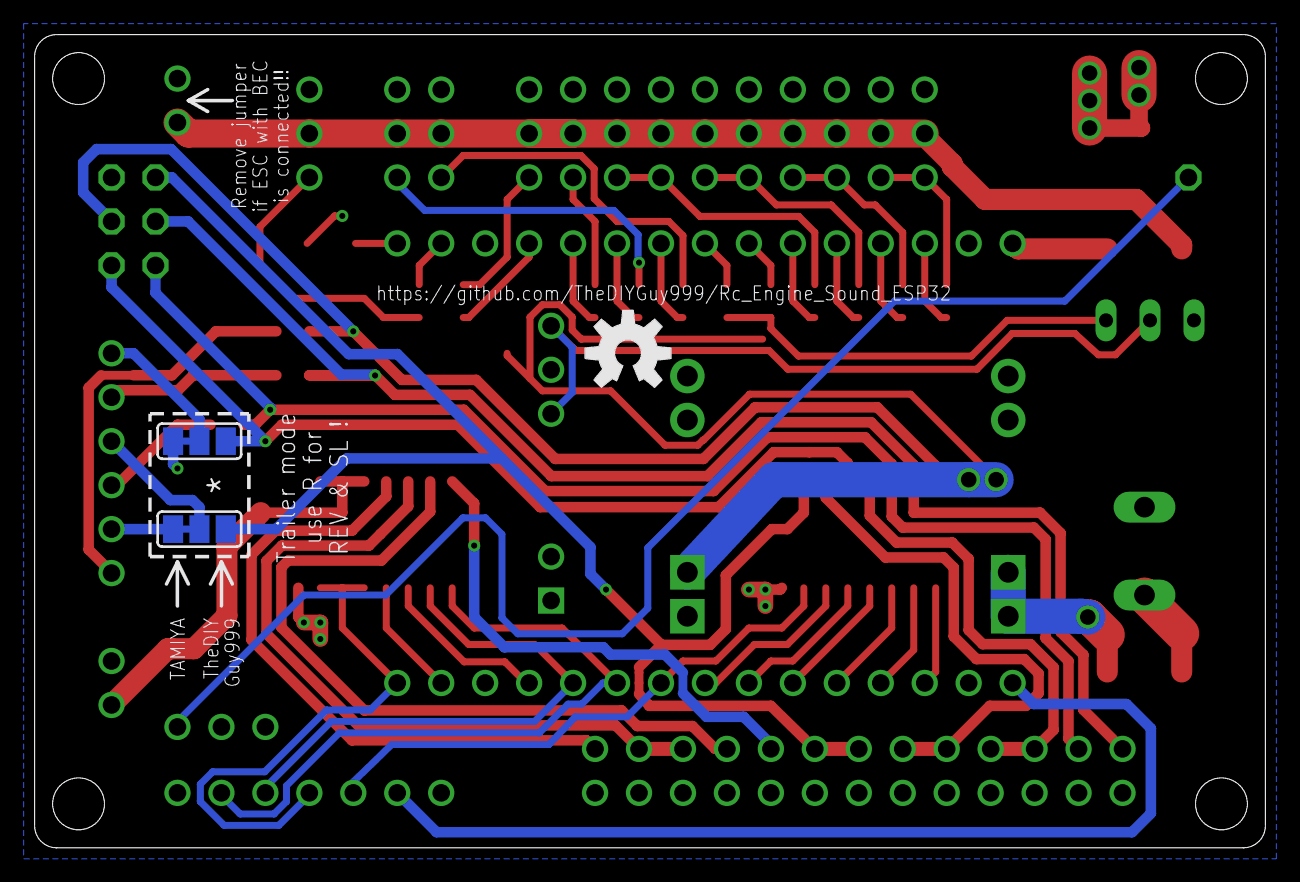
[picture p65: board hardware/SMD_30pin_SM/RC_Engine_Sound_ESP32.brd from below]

Board: 2 copper layers, 71.1 x 47.0 mm, 63 parts (3 on the bottom side), 60 nets.

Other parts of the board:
LOGO2: OSHW-LOGOM; OSHW-LOGO-M

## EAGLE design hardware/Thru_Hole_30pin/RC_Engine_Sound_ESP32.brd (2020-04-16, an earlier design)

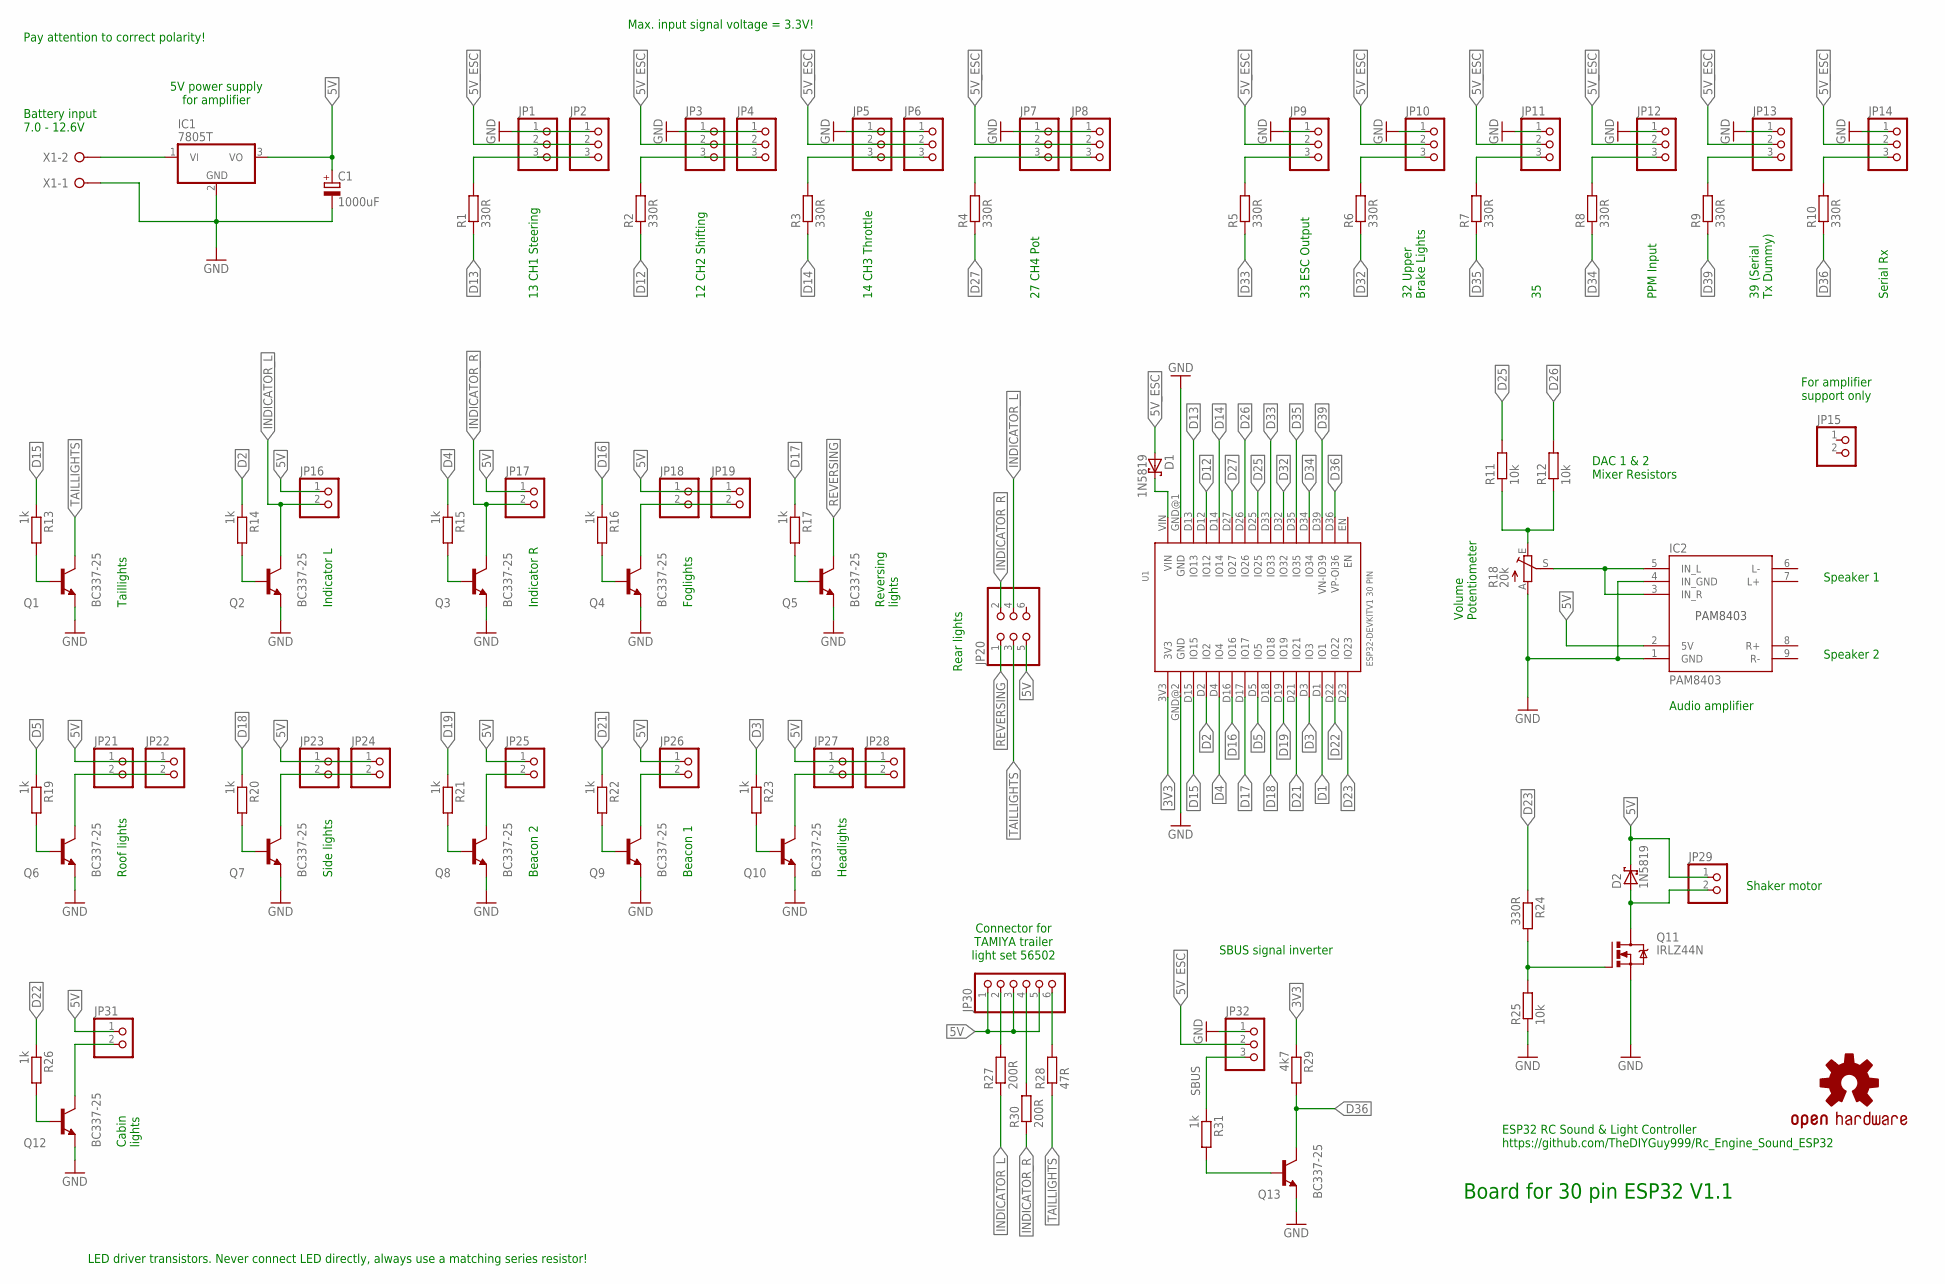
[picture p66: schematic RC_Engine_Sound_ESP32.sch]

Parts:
C1: 1000uF; E5-10,5
D1, D2: 1N5819; DO35-7
IC1: 7805T; TO220H
IC2: PAM8403
JP1, JP2, JP3, JP4, JP5, JP6, JP7, JP8, JP9, JP10, JP11, JP12, JP13, JP14, JP32: PINHD-1X3; 1X03
JP15, JP16, JP17, JP18, JP19, JP21, JP22, JP23, JP24, JP25, JP26, JP27, JP28, JP29, JP31: PINHD-1X2; 1X02
JP20: PINHD-2X3; 2X03
JP30: PINHD-1X6; 1X06
LOGO1: OSHW-LOGOM; OSHW-LOGO-M
Q1, Q2, Q3, Q4, Q5, Q6, Q7, Q8, Q9, Q10, Q12, Q13: BC337-25; TO92
Q11: IRLZ44N; TO220BV
R1, R2, R3, R4, R5, R6, R7, R8, R9, R10, R24: 330R; 0207/2V
R11, R12: 10k; 0207/10
R13, R14, R15, R16, R17, R19, R20, R21, R22, R23, R26, R31: 1k; 0207/2V
R18: 20k; S64W
R25: 10k; 0207/2V
R27, R30: 200R; 0207/10
R28: 47R; 0207/10
R29: 4k7; 0207/2V
U1: ESP32DEVKITV1; ESP32-DEVKITV1
X1: W237-02P; W237-132

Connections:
3V3: R29.1, U1.3V3
5V: C1.+, D2.C, IC1.3 (VO), IC2.2 (5V), JP16.1, JP17.1, JP18.1, JP19.1, JP20.5, JP21.1, JP22.1, JP23.1, JP24.1, JP25.1, JP26.1, JP27.1, JP28.1, JP29.1, JP30.1, JP30.3, JP30.5, JP31.1
5V_ESC: D1.A, JP1.2, JP2.2, JP3.2, JP4.2, JP5.2, JP6.2, JP7.2, JP8.2, JP9.2, JP10.2, JP11.2, JP12.2, JP13.2, JP14.2, JP32.2
BAT+: IC1.1 (VI), X1.2
D1: U1.D1 (IO1)
D2: R14.1, U1.D2 (IO2)
D3: R23.1, U1.D3 (IO3)
D4: R15.1, U1.D4 (IO4)
D5: R19.1, U1.D5 (IO5)
D12: R2.1, U1.D12 (IO12)
D13: R1.1, U1.D13 (IO13)
D14: R3.1, U1.D14 (IO14)
D15: R13.1, U1.D15 (IO15)
D16: R16.1, U1.D16 (IO16)
D17: R17.1, U1.D17 (IO17)
D18: R20.1, U1.D18 (IO18)
D19: R21.1, U1.D19 (IO19)
D21: R22.1, U1.D21 (IO21)
D22: R26.1, U1.D22 (IO22)
D23: R24.1, U1.D23 (IO23)
D25: R11.2, U1.D25 (IO25)
D26: R12.2, U1.D26 (IO26)
D27: R4.1, U1.D27 (IO27)
D32: R6.1, U1.D32 (IO32)
D33: R5.1, U1.D33 (IO33)
D34: R8.1, U1.D34 (IO34)
D35: R7.1, U1.D35 (IO35)
D36: Q13.3 (C), R10.1, R29.2, U1.D36 (VP-OI36)
D39: R9.1, U1.D39 (VN-IO39)
GND: C1.-, IC1.2 (GND), IC2.1 (GND), IC2.4 (IN_GND), JP1.1, JP2.1, JP3.1, JP4.1, JP5.1, JP6.1, JP7.1, JP8.1, JP9.1, JP10.1, JP11.1, JP12.1, JP13.1, JP14.1, JP32.1, Q1.1 (E), Q2.1 (E), Q3.1 (E), Q4.1 (E), Q5.1 (E), Q6.1 (E), Q7.1 (E), Q8.1 (E), Q9.1 (E), Q10.1 (E), Q11.S, Q12.1 (E), Q13.1 (E), R18.A, R25.1, U1.GND@1 (GND), U1.GND@2 (GND), X1.1
INDICATOR_L: JP16.2, JP20.4, Q2.3 (C), R27.1
INDICATOR_R: JP17.2, JP20.2, Q3.3 (C), R30.1
unnamed: IC2.3 (IN_R), IC2.5 (IN_L), R18.S
unnamed: R11.1, R12.1, R18.E
unnamed: JP1.3, JP2.3, R1.2
unnamed: Q11.G, R24.2, R25.2
unnamed: JP3.3, JP4.3, R2.2
unnamed: JP5.3, JP6.3, R3.2
unnamed: JP7.3, JP8.3, R4.2
unnamed: JP9.3, R5.2
unnamed: D1.C, U1.VIN
unnamed: JP10.3, R6.2
unnamed: JP11.3, R7.2
unnamed: JP12.3, R8.2
unnamed: JP13.3, R9.2
unnamed: JP14.3, R10.2
unnamed: D2.A, JP29.2, Q11.D
unnamed: Q10.2 (B), R23.2
unnamed: Q4.2 (B), R16.2
unnamed: JP27.2, JP28.2, Q10.3 (C)
unnamed: JP18.2, JP19.2, Q4.3 (C)
unnamed: Q1.2 (B), R13.2
unnamed: JP30.2, R27.2
unnamed: Q2.2 (B), R14.2
unnamed: JP30.4, R30.2
unnamed: Q3.2 (B), R15.2
unnamed: JP30.6, R28.2
unnamed: Q5.2 (B), R17.2
unnamed: Q6.2 (B), R19.2
unnamed: JP21.2, JP22.2, Q6.3 (C)
unnamed: Q7.2 (B), R20.2
unnamed: JP23.2, JP24.2, Q7.3 (C)
unnamed: Q8.2 (B), R21.2
unnamed: JP25.2, Q8.3 (C)
unnamed: Q9.2 (B), R22.2
unnamed: JP26.2, Q9.3 (C)
unnamed: Q12.2 (B), R26.2
unnamed: JP31.2, Q12.3 (C)
unnamed: Q13.2 (B), R31.2
REVERSING: JP20.1, Q5.3 (C)
SBUS: JP32.3, R31.1
TAILLIGHTS: JP20.3, Q1.3 (C), R28.1

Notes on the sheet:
Speaker 1
Speaker 2
13 CH1 Steering
12 CH2 Shifting
14 CH3 Throttle
27 CH4 Pot
33 ESC Output
32 Upper Brake Lights
PPM Input
39 (Serial Tx Dummy)
Serial Rx
DAC 1 & 2 Mixer Resistors
Audio amplifier
Volume Potentiometer
5V power supply for amplifier
Battery input 7.0 - 12.6V
Board for 30 pin ESP32 V1.1
Shaker motor
Headlights
Foglights
Taillights
Indicator L
Indicator R
Roof lights
Side lights
Reversing lights
Connector for TAMIYA trailer light set 56502
Rear lights
ESP32 RC Sound & Light Controller https://github.com/TheDIYGuy999/Rc_Engine_Sound_ESP32
LED driver transistors. Never connect LED directly, always use a matching series resistor!
Beacon 2
Beacon 1
Cabin lights
SBUS signal inverter
For amplifier support only
Pay attention to correct polarity!
Max. input signal voltage = 3.3V!

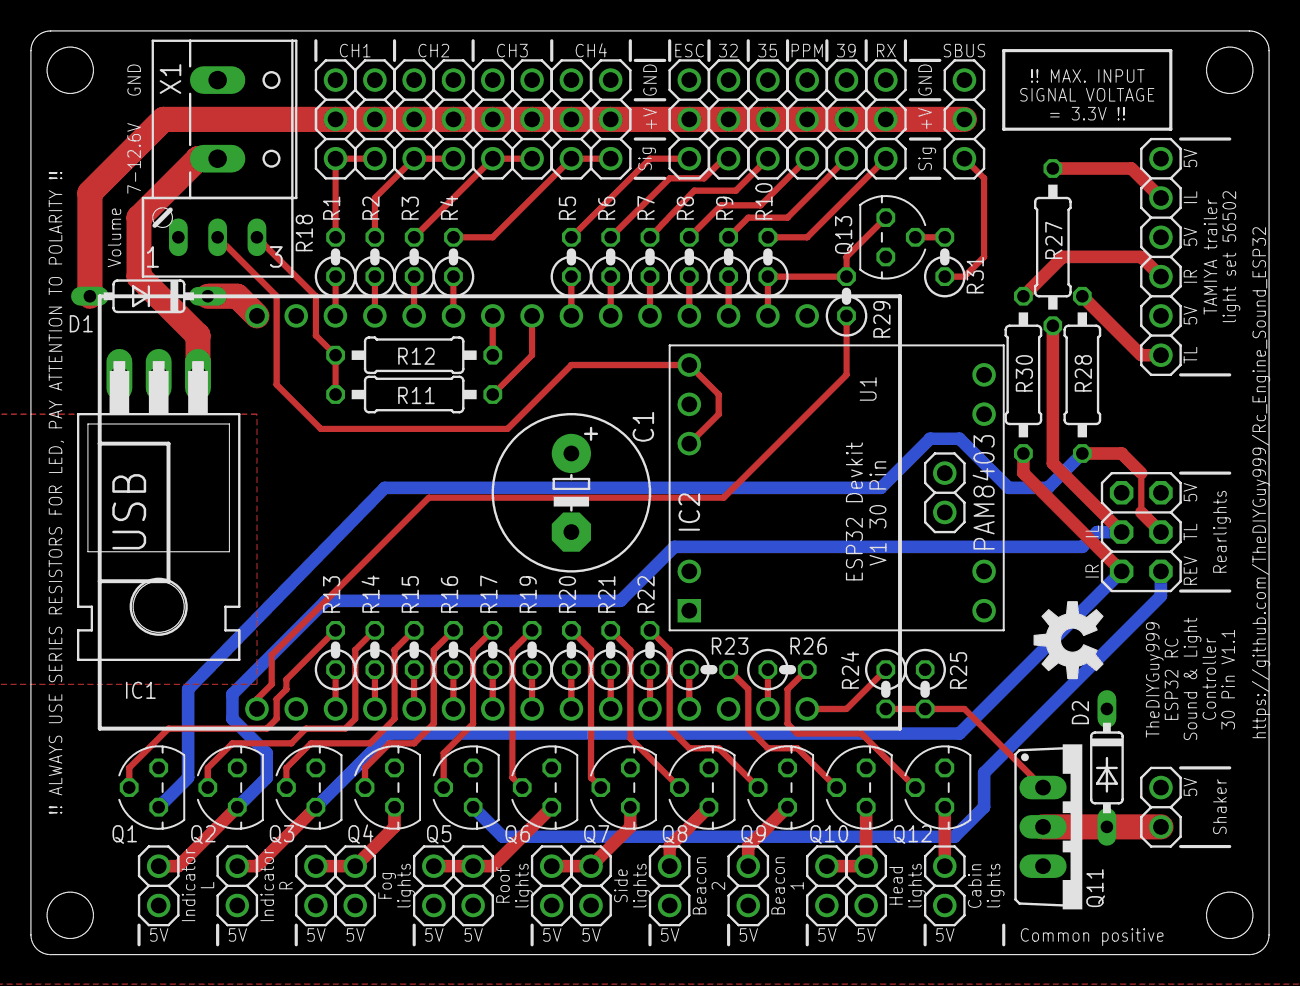
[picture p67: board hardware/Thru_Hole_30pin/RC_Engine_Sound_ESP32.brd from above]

Board: 2 copper layers, 80.0 x 59.7 mm, 84 parts (0 on the bottom side), 71 nets.

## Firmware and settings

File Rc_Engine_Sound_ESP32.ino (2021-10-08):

/* RC engine sound & LED controller for Arduino ESP32. Written by TheDIYGuy999
    Based on the code for ATmega 328: https://github.com/TheDIYGuy999/Rc_Engine_Sound

 *  ***** ESP32 CPU frequency must be set to 240MHz! *****
    ESP32 macOS Big Sur fix see: https://github.com/TheDIYGuy999/Rc_Engine_Sound_ESP32/blob/master/BigSurFix.md

   Sound files converted with: https://github.com/TheDIYGuy999/Rc_Engine_Sound_ESP32/blob/master/Audio2Header.html
   Original converter code by bitluni (send him a high five, if you like the code)

   Parts of automatic transmision code from Wombii's fork: https://github.com/Wombii/Rc_Engine_Sound_ESP32

   Dashboard, Neopixel and SUMD support by Gamadril: https://github.com/Gamadril/Rc_Engine_Sound_ESP32
*/

const float codeVersion = 8.11; // Software revision.

//
// =======================================================================================================
// ERROR CODES (INDICATOR LIGHTS)
// =======================================================================================================
//
/* Constantly on = no SBUS signal (check "sbusInverted" true / false in "2_adjustmentsRemote.h")
   Number of blinks = this channel signal is not between 1400 and 1600 microseconds and can't be auto calibrated
   (check channel trim settings)
*/

//
// =======================================================================================================
// ! ! I M P O R T A N T ! !   ALL USER SETTINGS ARE DONE IN THE FOLLOWING TABS, WHICH ARE DISPLAYED ABOVE
// (ADJUST THEM BEFORE CODE UPLOAD), DO NOT CHANGE ANYTHING IN THIS TAB EXCEPT THE DEBUG OPTIONS
// =======================================================================================================
//

// All the required user settings are done in the following .h files:
#include "1_adjustmentsVehicle.h"       // <<------- Select the vehicle you want to simulate
#include "2_adjustmentsRemote.h"        // <<------- Remote control system related adjustments
#include "3_adjustmentsESC.h"           // <<------- ESC related adjustments
#include "4_adjustmentsTransmission.h"  // <<------- Transmission related adjustments
#include "5_adjustmentsShaker.h"        // <<------- Shaker related adjustments
#include "6_adjustmentsLights.h"        // <<------- Lights related adjustments
#include "7_adjustmentsServos.h"        // <<------- Servo output related adjustments
#include "8_adjustmentsSound.h"         // <<------- Sound related adjustments
#include "9_adjustmentsDashboard.h"     // <<------- Dashboard related adjustments

// DEBUG options can slow down the playback loop! Only uncomment them for debugging, may slow down your system!
//#define CHANNEL_DEBUG // uncomment it for input signal debugging informations
//#define ESC_DEBUG // uncomment it to debug the ESC
//#define AUTO_TRANS_DEBUG // uncomment it to debug the automatic transmission
//#define MANUAL_TRANS_DEBUG // uncomment it to debug the manual transmission
//#define TRACKED_DEBUG // debugging tracked vehicle mode
//#define SERVO_DEBUG // uncomment it for servo calibration in BUS communication mode

// TODO = Things to clean up!

//
// =======================================================================================================
// LIRBARIES & HEADER FILES, REQUIRED ESP32 BOARD DEFINITION
// =======================================================================================================
//

// Header files
#include "headers/curves.h" // Nonlinear throttle curve arrays

// Libraries (you have to install all of them in the "Arduino sketchbook"/libraries folder)
// !! Do NOT install the libraries in the sketch folder.
#include <statusLED.h> // https://github.com/TheDIYGuy999/statusLED <<------- required for LED control
#include <SBUS.h>      // https://github.com/TheDIYGuy999/SBUS      <<------- you need to install my fork of this library!
#include <rcTrigger.h> // https://github.com/TheDIYGuy999/rcTrigger <<------- required for RC signal processing
#include <IBusBM.h>    // https://github.com/bmellink/IBusBM        <<------- required for IBUS interface
#include <TFT_eSPI.h>  // https://github.com/Bodmer/TFT_eSPI        <<------- required for LCD dashboard
#include <FastLED.h>   // https://github.com/FastLED/FastLED        <<------- required for Neopixel support

// Plugins (included, but not programmed by TheDIYGuy999)
#include "src/dashboard.h" // For LCD dashboard. See: https://github.com/Gamadril/Rc_Engine_Sound_ESP32
#include "src/SUMD.h"      // For Graupner SUMD interface. See: https://github.com/Gamadril/Rc_Engine_Sound_ESP32

// No need to install these, they come with the ESP32 board definition
#include "driver/rmt.h"   // for PWM signal detection
#include "driver/mcpwm.h" // for servo PWM output
#include "soc/rtc_wdt.h"  // for watchdog timer

// Install ESP32 board according to: https://randomnerdtutorials.com/installing-the-esp32-board-in-arduino-ide-windows-instructions/
// Warning: do not use Espressif ESP32 board definition v1.05, its causing crash & reboot loops! Use v1.04 instead.
// Adjust board settings according to: https://github.com/TheDIYGuy999/Rc_Engine_Sound_ESP32/blob/master/pictures/settings.png

// Make sure to remove -master from your sketch folder name

//
// =======================================================================================================
// PIN ASSIGNMENTS & GLOBAL VARIABLES (Do not play around here)
// =======================================================================================================
//
// Pin assignment and wiring instructions ****************************************************************

// ------------------------------------------------------------------------------------
// Use a 330Ohm resistor in series with all I/O pins! allows to drive LED directly and
// provides short circuit protection. Also works on the serial Rx pin "VP" (36)
// ------------------------------------------------------------------------------------

// Serial command pins for SBUS & IBUS -----
#define COMMAND_RX 36 // pin 36, labelled with "VP", connect it to "Micro RC Receiver" pin "TXO"
#define COMMAND_TX 39 // pin 39, labelled with "VN", only used as a dummy, not connected

// PPM signal pin (multiple channel input with only one wire) -----
#define PPM_PIN 36

// PWM RC signal pins (active, if no other communications profile is enabled) -----
// Channel numbers may be different on your recveiver!
//CH1: (steering)
//CH2: (gearbox) (left throttle in TRACKED_MODE)
//CH3: (throttle) (right throttle in TRACKED_MODE)
//CH4: (horn and bluelight / siren)
//CH5: (high / low beam, transmission neutral, jake brake etc.)
//CH6: (indicators, hazards)
#define PWM_CHANNELS_NUM 6 // Number of PWM signal input pins 6
const uint8_t PWM_CHANNELS[PWM_CHANNELS_NUM] = { 1, 2, 3, 4, 5, 6}; // Channel numbers
const uint8_t PWM_PINS[PWM_CHANNELS_NUM] = { 13, 12, 14, 27, 35, 34 }; // Input pin numbers

#define ESC_OUT_PIN 33 // connect crawler type ESC here (working fine, but use it at your own risk! Not supported in TRACKED_MODE) -----

#define STEERING_PIN 13 // CH1 output for steering servo (bus communication only)
#define SHIFTING_PIN 12 // CH2 output for shifting servo (bus communication only)
#define WINCH_PIN 14 // CH3 output for winch servo (bus communication only)
#define COUPLER_PIN 27 // CH4 output for coupler (5th. wheel) servo (bus communication only)

#ifdef PROTOTYPE_36 // switching headlight pin depending on the board variant (do not uncomment it, or it will cause boot issues!)
#define HEADLIGHT_PIN 0 // White headllights connected to pin D0, which only exists on the 36 pin ESP32 board (causes boot issues, if used!)
#else
#define HEADLIGHT_PIN 3 // 3 = RX0 pin, (1 = TX0 is not usable) white headllights
#endif

#define TAILLIGHT_PIN 15 // Red tail- & brake-lights (combined)
#define INDICATOR_LEFT_PIN 2 // Orange left indicator (turn signal) light
#define INDICATOR_RIGHT_PIN 4 // Orange right indicator (turn signal) light
#define FOGLIGHT_PIN 16 // (16 = RX2) Fog lights
#define REVERSING_LIGHT_PIN 17 // (TX2) White reversing light
#define ROOFLIGHT_PIN 5 // Roof lights (high beam, if "define SEPARATE_FULL_BEAM")
#define SIDELIGHT_PIN 18 // Side lights (connect roof ligthts here, if "define SEPARATE_FULL_BEAM")
#define BEACON_LIGHT2_PIN 19 // Blue beacons light
#define BEACON_LIGHT1_PIN 21 // Blue beacons light
#define CABLIGHT_PIN 22 // Cabin lights

#define RGB_LEDS_PIN 0 // Pin is used for WS2812 LED control

#if defined THIRD_BRAKLELIGHT
#define BRAKELIGHT_PIN 32 // Upper brake lights
#else
#define COUPLER_SWITCH_PIN 32 // switch for trailer coupler sound
#endif

#define SHAKER_MOTOR_PIN 23 // Shaker motor (shaking truck while idling and engine start / stop)

#define DAC1 25 // connect pin25 (do not change the pin) to a 10kOhm resistor
#define DAC2 26 // connect pin26 (do not change the pin) to a 10kOhm resistor
// both outputs of the resistors above are connected together and then to the outer leg of a
// 10kOhm potentiometer. The other outer leg connects to GND. The middle leg connects to both inputs
// of a PAM8403 amplifier and allows to adjust the volume. This way, two speakers can be used.

// Objects *************************************************************************************
// Status LED objects (also used for PWM shaker motor and ESC control) -----
statusLED headLight(false); // "false" = output not inversed
statusLED tailLight(false);
statusLED indicatorL(false);
statusLED indicatorR(false);
statusLED fogLight(false);
statusLED reversingLight(false);
statusLED roofLight(false);
statusLED sideLight(false);
statusLED beaconLight1(false);
statusLED beaconLight2(false);
statusLED shakerMotor(false);
statusLED cabLight(false);
statusLED brakeLight(false);

statusLED escOut(false);

// rcTrigger objects -----
// Analog or 3 position switches (short / long pressed time)
rcTrigger functionR100u(200); // 200ms required!
rcTrigger functionR100d(100);
rcTrigger functionR75u(300); // 300ms required!
rcTrigger functionR75d(300); // 300ms required!
rcTrigger functionL100l(100);
rcTrigger functionL100r(100);
rcTrigger functionL75l(300); // 300ms required!
rcTrigger functionL75r(300); // 300ms required!

// Latching 2 position
rcTrigger mode1Trigger(100);
rcTrigger mode2Trigger(100);

// momentary buttons
rcTrigger momentary1Trigger(100);

// Flags
rcTrigger hazardsTrigger(100);
rcTrigger indicatorLTrigger(100);
rcTrigger indicatorRTrigger(100);

// Dashboard
Dashboard dashboard;

// Neopixel
#define RGB_LEDS_COUNT 1
CRGB rgbLEDs[RGB_LEDS_COUNT];

// Global variables **********************************************************************

// PWM processing variables
#define RMT_TICK_PER_US 1
// determines how many clock cycles one "tick" is
// [1..255], source is generally 80MHz APB clk
#define RMT_RX_CLK_DIV (80000000/RMT_TICK_PER_US/1000000)
// time before receiver goes idle (longer pulses will be ignored)
#define RMT_RX_MAX_US 3500
volatile uint16_t pwmBuf[PWM_CHANNELS_NUM] = {0};
uint32_t maxPwmRpmPercentage = 390; // Limit required to prevent controller from crashing @ high engine RPM

// PPM signal processing variables
#define NUM_OF_PPM_CHL 8 // The number of channels inside our PPM signal (8 is the maximum!)
#define NUM_OF_PPM_AVG 1 // Number of averaging passes (usually one, more will be slow)
volatile int ppmInp[NUM_OF_PPM_CHL + 1] = {0}; // Input values
volatile int ppmBuf[16] = {0}; // Buffered values TODO, was [NUM_OF_PPM_CHL + 1]
volatile byte counter = NUM_OF_PPM_CHL;
volatile byte average  = NUM_OF_PPM_AVG;
volatile boolean ready = false;
volatile unsigned long timelast;
unsigned long timelastloop;
uint32_t maxPpmRpmPercentage = 390; // Limit required to prevent controller from crashing @ high engine RPM

// SBUS signal processing variables
SBUS sBus(Serial2); // SBUS object on Serial 2 port
// channel, fail safe, and lost frames data
uint16_t SBUSchannels[16];
bool SBUSfailSafe;
bool SBUSlostFrame;
bool sbusInit;
uint32_t maxSbusRpmPercentage = 390; // Limit required to prevent controller from crashing @ high engine RPM

// SUMD signal processing variables
HardwareSerial serial(2);
SUMD sumd(serial); // SUMD object on Serial 2 port
// channel, fail safe, and lost frames data
uint16_t SUMDchannels[16]; // only 12 are usable!
bool SUMD_failsafe;
bool SUMD_frame_lost;
bool SUMD_init;
uint32_t maxSumdRpmPercentage = 390; // Limit required to prevent controller from crashing @ high engine RPM

// IBUS signal processing variables
IBusBM iBus;    // IBUS object
bool ibusInit;
uint32_t maxIbusRpmPercentage = 340; // Limit required to prevent controller from crashing @ high engine RPM (was 350, but sometimes crashing)

// Interrupt latches
volatile boolean couplerSwitchInteruptLatch; // this is enabled, if the coupler switch pin change interrupt is detected

// Control input signals
#define PULSE_ARRAY_SIZE 14                              // 13 channels (+ the unused CH0)
uint16_t pulseWidthRaw[PULSE_ARRAY_SIZE];                // Current RC signal RAW pulse width [X] = channel number
uint16_t pulseWidthRaw2[PULSE_ARRAY_SIZE];               // Current RC signal RAW pulse width with linearity compensation [X] = channel number
uint16_t pulseWidth[PULSE_ARRAY_SIZE];                   // Current RC signal pulse width [X] = channel number
int16_t pulseOffset[PULSE_ARRAY_SIZE];                   // Offset for auto zero adjustment

uint16_t pulseMaxNeutral[PULSE_ARRAY_SIZE];              // PWM input signal configuration storage variables
uint16_t pulseMinNeutral[PULSE_ARRAY_SIZE];
uint16_t pulseMax[PULSE_ARRAY_SIZE];
uint16_t pulseMin[PULSE_ARRAY_SIZE];
uint16_t pulseMaxLimit[PULSE_ARRAY_SIZE];
uint16_t pulseMinLimit[PULSE_ARRAY_SIZE];

uint16_t pulseZero[PULSE_ARRAY_SIZE];                    // Usually 1500 (The mid point of 1000 - 2000 Microseconds)
uint16_t pulseLimit = 1100;                              // pulseZero +/- this value (1100)
uint16_t pulseMinValid = 700;                            // The minimum valid pulsewidth (was 950)
uint16_t pulseMaxValid = 2300;                           // The maximum valid pulsewidth (was 2050)
bool autoZeroDone;                                       // Auto zero offset calibration done
#define NONE 16                                          // The non existing "Dummy" channel number (usually 16) TODO

volatile boolean failSafe = false;                       // Triggered in emergency situations like: throttle signal lost etc.

boolean mode1;                                           // Signal state variables
boolean mode2;
boolean momentary1;
boolean hazard;
boolean left;
boolean right;
boolean unlock5thWheel;
boolean winchPull;
boolean winchRelease;

boolean winchEnabled;

// Sound
volatile boolean engineOn = false;                       // Signal for engine on / off
volatile boolean engineStart = false;                    // Active, if engine is starting up
volatile boolean engineRunning = false;                  // Active, if engine is running
volatile boolean engineStop = false;                     // Active, if engine is shutting down
volatile boolean jakeBrakeRequest = false;               // Active, if engine jake braking is requested
volatile boolean engineJakeBraking = false;              // Active, if engine is jake braking
volatile boolean wastegateTrigger = false;               // Trigger wastegate (blowoff) after rapid throttle drop
volatile boolean blowoffTrigger = false;                 // Trigger jake brake sound (blowoff) after rapid throttle drop
volatile boolean dieselKnockTrigger = false;             // Trigger Diesel ignition "knock"
volatile boolean dieselKnockTriggerFirst = false;        // The first  Diesel ignition "knock" per sequence
volatile boolean airBrakeTrigger = false;                // Trigger for air brake noise
volatile boolean parkingBrakeTrigger = false;            // Trigger for air parking brake noise
volatile boolean shiftingTrigger = false;                // Trigger for shifting noise
volatile boolean hornTrigger = false;                    // Trigger for horn on / off
volatile boolean sirenTrigger = false;                   // Trigger for siren  on / off
volatile boolean sound1trigger = false;                  // Trigger for sound1  on / off
volatile boolean couplingTrigger = false;                // Trigger for trailer coupling  sound
volatile boolean uncouplingTrigger = false;              // Trigger for trailer uncoupling  sound
volatile boolean bucketRattleTrigger = false;            // Trigger for bucket rattling  sound
volatile boolean indicatorSoundOn = false;               // active, if indicator bulb is on

// Sound latches
volatile boolean hornLatch = false;                      // Horn latch bit
volatile boolean sirenLatch = false;                     // Siren latch bit

// Sound volumes
volatile uint16_t throttleDependentVolume = 0;           // engine volume according to throttle position
volatile uint16_t throttleDependentRevVolume = 0;        // engine rev volume according to throttle position
volatile uint16_t rpmDependentJakeBrakeVolume = 0;       // Engine rpm dependent jake brake volume
volatile uint16_t throttleDependentKnockVolume = 0;      // engine Diesel knock volume according to throttle position
volatile uint16_t rpmDependentKnockVolume = 0;           // engine Diesel knock volume according to engine RPM
volatile uint16_t throttleDependentTurboVolume = 0;      // turbo volume according to rpm
volatile uint16_t throttleDependentFanVolume = 0;        // cooling fan volume according to rpm
volatile uint16_t throttleDependentChargerVolume = 0;    // cooling fan volume according to rpm
volatile uint16_t rpmDependentWastegateVolume = 0;       // wastegate volume according to rpm
volatile uint16_t tireSquealVolume = 0;                  // Tire squeal volume according to speed and cornering radius
// for excavator mode:
volatile uint16_t hydraulicPumpVolume = 0;               // hydraulic pump volume
volatile uint16_t hydraulicFlowVolume = 0;               // hydraulic flow volume
volatile uint16_t trackRattleVolume = 0;                 // track rattling volume
volatile uint16_t hydraulicDependentKnockVolume = 100;   // engine Diesel knock volume according to hydraulic load
volatile uint16_t hydraulicLoad = 0;                     // Hydraulic load dependent RPM drop

volatile int16_t masterVolume = 100;                     // Master volume percentage
volatile uint8_t dacOffset = 0;  // 128, but needs to be ramped up slowly to prevent popping noise, if switched on

// Throttle
int16_t currentThrottle = 0;                             // 0 - 500 (Throttle trigger input)
int16_t currentThrottleFaded = 0;                        // faded throttle for volume calculations etc.

// Engine
const int16_t maxRpm = 500;                              // always 500
const int16_t minRpm = 0;                                // always 0
int32_t currentRpm = 0;                                  // 0 - 500 (signed required!)
volatile uint8_t engineState = 0;                        // Engine state
enum EngineState                                         // Engine state enum
{
  OFF,
  STARTING,
  RUNNING,
  STOPPING,
  PARKING_BRAKE
};
int16_t engineLoad = 0;                                  // 0 - 500
volatile uint16_t engineSampleRate = 0;                  // Engine sample rate
int32_t speedLimit = maxRpm;                             // The speed limit, depending on selected virtual gear

// Clutch
boolean clutchDisengaged = true;                         // Active while clutch is disengaged
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
void loop() {

#if defined SBUS_COMMUNICATION
  readSbusCommands(); // SBUS communication (pin 36)
  mcpwmOutput(); // PWM servo signal output

#elif defined IBUS_COMMUNICATION
  readIbusCommands(); // IBUS communication (pin 36)
  mcpwmOutput(); // PWM servo signal output

#elif defined SUMD_COMMUNICATION
  readSumdCommands(); // SUMD communication (pin 36)
  mcpwmOutput(); // PWM servo signal output

#elif defined PPM_COMMUNICATION
  readPpmCommands(); // PPM communication (pin 34)
  mcpwmOutput(); // PWM servo signal output

#else
  // measure RC signals mark space ratio
  readPwmSignals();
#endif

  // Map pulsewidth to throttle
  mapThrottle();

  // Horn triggering
  triggerHorn();

  // Indicator (turn signal) triggering
  triggerIndicators();

  // rcTrigger
  rcTrigger();

  // Excavator specific controls
#if defined EXCAVATOR_MODE
  excavatorControl();
#endif

  // Read trailer switch state
#if not defined THIRD_BRAKLELIGHT
  trailerPresenceSwitchRead();
#endif

  // Dashboard control
#if defined SPI_DASHBOARD
  updateDashboard();
#endif

  // RGB LED control
#if defined NEOPIXEL_LED
  updateRGBLEDs();
#endif

  // Feeding the RTC watchtog timer is essential!
  rtc_wdt_feed();
}

//
// =======================================================================================================
// 1st MAIN TASK, RUNNING ON CORE 0 (Interrupts are running on this core as well)
// =======================================================================================================
//

void Task1code(void *pvParameters) {
  for (;;) {

    // DAC offset fader
    dacOffsetFade();

    // Simulate engine mass, generate RPM signal
    engineMassSimulation();

    // Call gear selector
    if (automatic || doubleClutch) automaticGearSelector();

    // Switch engine on or off
    engineOnOff();

    // LED control
    if (autoZeroDone) led();

#if not defined SPI_DASHBOARD
    // Shaker control
    shaker();
#endif

    // Gearbox detection
    gearboxDetection();

    // ESC control (Crawler ESC with direct brake on pin 33)
    esc();

    // measure loop time
    //loopTime = loopDuration(); // for debug only
  }
}

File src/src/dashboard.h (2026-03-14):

#include "Arduino.h"
#include <TFT_eSPI.h> // https://github.com/Bodmer/TFT_eSPI

//#define FREVIC_DASHBOARD // Define this, if you awant to use the nice alternative dashboard from Frevic

#ifndef FREVIC_DASHBOARD // Standard dashboard *********************************************************************************************************************
/*
 * dashboard.h - Library to drive a 80x160px color LCD as rc truck dashboard
 *
 * https://github.com/Gamadril/Rc_Engine_Sound_ESP32
 * MIT License
 */

#ifndef DASHBOARD_h
#define DASHBOARD_h

#define SCREEN_WIDTH 160
#define SCREEN_HEIGHT 80
#define DEG2RAD 0.0174532925
#define SPEED_MIN 0
#define SPEED_MAX 120
#define RPM_MIN 0
#define RPM_MAX 500
#define FUEL_MIN 0
#define FUEL_MAX 100
#define ADBLUE_MIN 0
#define ADBLUE_MAX 100

#define SPEED_CIRCLE_CENTER_X 40
#define SPEED_CIRCLE_CENTER_Y 35
#define SPEED_CIRCLE_RADIUS 25
#define SPEED_NEEDLE_LENGTH 20
#define SPEED_CIRCLE_ANGLE_START -203 // -180 - 23
#define SPEED_CIRCLE_SEGMENTS 12
#define SPEED_CIRCLE_SEGMENT_ANGLE 18.95
#define SPEED_CIRCLE_ANGLE_END \
    SPEED_CIRCLE_ANGLE_START + SPEED_CIRCLE_SEGMENTS *SPEED_CIRCLE_SEGMENT_ANGLE

#define RPM_CIRCLE_CENTER_X SCREEN_WIDTH - 40
#define RPM_CIRCLE_CENTER_Y 35
#define RPM_CIRCLE_RADIUS 25
#define RPM_CIRCLE_ANGLE_START -202 // -180 - 22
#define RPM_CIRCLE_SEGMENTS 25
#define RPM_CIRCLE_SEGMENT_ANGLE 9
#define RPM_CIRCLE_ANGLE_END RPM_CIRCLE_ANGLE_START + RPM_CIRCLE_SEGMENTS *RPM_CIRCLE_SEGMENT_ANGLE

#define FUEL_CIRCLE_CENTER_X 30
#define FUEL_CIRCLE_CENTER_Y 60
#define FUEL_CIRCLE_RADIUS 14
#define FUEL_CIRCLE_ANGLE_START -202 // -180 - 22
#define FUEL_CIRCLE_SEGMENTS 16
#define FUEL_CIRCLE_SEGMENT_ANGLE 14
#define FUEL_CIRCLE_ANGLE_END \
    FUEL_CIRCLE_ANGLE_START + FUEL_CIRCLE_SEGMENTS *FUEL_CIRCLE_SEGMENT_ANGLE

#define ADBLUE_CIRCLE_CENTER_X SCREEN_WIDTH - 30
#define ADBLUE_CIRCLE_CENTER_Y 60
#define ADBLUE_CIRCLE_RADIUS 14
#define ADBLUE_CIRCLE_ANGLE_START -202 // -180 - 22
#define ADBLUE_CIRCLE_SEGMENTS 16
#define ADBLUE_CIRCLE_SEGMENT_ANGLE 14
#define ADBLUE_CIRCLE_ANGLE_END \
    ADBLUE_CIRCLE_ANGLE_START + ADBLUE_CIRCLE_SEGMENTS *ADBLUE_CIRCLE_SEGMENT_ANGLE

#define INDICATOR_LEFT_CENTER_X SCREEN_WIDTH / 2 - 20
#define INDICATOR_LEFT_CENTER_Y 9

#define INDICATOR_RIGHT_CENTER_X SCREEN_WIDTH / 2 + 20
#define INDICATOR_RIGHT_CENTER_Y 9

// CUSTOM COLOR DEFINITIONS
// http://www.rinkydinkelectronics.com/calc_rgb565.php
#define offColor 0x2104 // indicators off (very dark grey)
#define backColor 0x0026
#define gaugeColor 0x055D
#define dataColor 0x0311
#define purple 0xEA16
#define needleColor 0xF811

const uint8_t LOW_BEAM_ICON[7][13] PROGMEM = {
    {1, 1, 0, 0, 0, 0, 0, 0, 0, 0, 0, 1, 1},
    {0, 1, 1, 1, 1, 0, 0, 0, 1, 1, 1, 1, 0},
    {0, 0, 1, 0, 1, 1, 0, 1, 1, 0, 1, 0, 0},
    {1, 1, 1, 0, 0, 1, 0, 1, 0, 0, 1, 1, 1},
    {0, 0, 1, 0, 1, 1, 0, 1, 1, 0, 1, 0, 0},
    {0, 1, 1, 1, 1, 0, 0, 0, 1, 1, 1, 1, 0},
    {1, 1, 0, 0, 0, 0, 0, 0, 0, 0, 0, 1, 1}};

const uint8_t HIGH_BEAM_ICON[7][13] PROGMEM = {
    {0, 0, 0, 0, 0, 0, 0, 1, 1, 1, 1, 0, 0},
    {1, 1, 1, 1, 1, 0, 1, 1, 0, 0, 1, 1, 0},
    {0, 0, 0, 0, 0, 0, 1, 0, 0, 0, 0, 1, 1},
    {1, 1, 1, 1, 1, 0, 1, 0, 0, 0, 0, 0, 1},
    {0, 0, 0, 0, 0, 0, 1, 0, 0, 0, 0, 1, 1},
    {1, 1, 1, 1, 1, 0, 1, 1, 0, 0, 1, 1, 0},
    {0, 0, 0, 0, 0, 0, 0, 1, 1, 1, 1, 0, 0}};

const uint8_t FOG_LIGHT_ICON[7][13] PROGMEM = {
    {0, 0, 0, 1, 1, 0, 0, 1, 1, 1, 1, 0, 0},
    {0, 1, 1, 1, 0, 0, 1, 1, 0, 0, 1, 1, 0},
    {1, 0, 1, 0, 1, 0, 1, 0, 0, 0, 0, 1, 1},
    {0, 1, 1, 1, 0, 0, 1, 0, 0, 0, 0, 0, 1},
    {1, 0, 0, 0, 1, 1, 1, 0, 0, 0, 0, 1, 1},
    {0, 1, 1, 1, 1, 0, 1, 1, 0, 0, 1, 1, 0},
    {1, 0, 1, 0, 0, 0, 0, 1, 1, 1, 1, 0, 0}};

const uint8_t PUMP_ICON[6][7] PROGMEM = {
    {0, 1, 1, 1, 1, 0, 0},
    {0, 1, 0, 0, 1, 1, 0},
    {0, 1, 0, 0, 1, 0, 1},
    {0, 1, 1, 1, 1, 1, 0},
    {0, 1, 1, 1, 1, 0, 0},
    {1, 1, 1, 1, 1, 1, 0}};
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

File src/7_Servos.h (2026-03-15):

#include <Arduino.h>

/* SERVO OUTPUT SETTINGS ************************************************************************************************
 *
 * The CH1 - CH6 headers are used as outputs in BUS communication mode (SBUS, IBUS, PPM)
 * This allows to use as super compact "bus-only" receiver
 * Set the endpoints here in 1000 - 2000 microseconds (equal to -45 to 45° servo angle)
 * !! WARNING: Don't connect a receiver to the "CH1 - CH6" headers, if BUS communication is selected. Ihis will short them out!!
 *
 * Uncommenting "#define SERVO_DEBUG" in the main tab allows to calibrate the servo positions easily:
 * 1. select the "SERVOS_DEFAULT" servo configuration
 * 2. upload the sketch
 * 3. connect the servo you want to calibrate to the steeting channel CH2 on the sound controller
 * 4. turn your steering wheel until you cave the position you want
 * 5. write down the microseconds reading, which is displayed in the Arduino IDE serial monitor
 * 6. do it for every position
 * 7. make a servo configuration profile, using these values
 * 8. select this profile and upload the sketch
 * 9. that's it!
 */

// Select the vehicle configuration you have:
// #define SERVOS_DEFAULT // <------- Select (remove //) one of the remote configurations below
// #define SERVOS_LANDY_MN_MODEL
// #define SERVOS_LANDY_DOUBLE_EAGLE
// #define SERVOS_C34
// #define SERVOS_URAL
// #define SERVOS_RGT_EX86100
// #define SERVOS_ACTROS
// #define SERVOS_KING_HAULER
// #define SERVOS_RACING_TRUCK
// #define SERVOS_MECCANO_DUMPER
// #define SERVOS_OPEN_RC_TRACTOR
// NOTICE: The following profiles are for EXCAVATOR_MODE only! ---------------------
 #define SERVOS_EXCAVATOR // For excavators with electric actuators
// #define SERVOS_HYDRAULIC_EXCAVATOR // For hydraulic excavators
// #define SERVOS_CRANE // For Mushroom3D rough terrain crane (servo outputs used as outrigger channels SBUS decoder)

// Default servo configuration profile -------------------------------------------------------------------------------------------
#ifdef SERVOS_DEFAULT

#define CH3_BEACON              // Rotating Beacons are connected to Servo CH3. BUS mode only! https://www.ebay.ch/itm/303979210629
#define MODE2_TRAILER_UNLOCKING // The mode 2 button is used for trailer unlocking by servo CH4 (sound1 triggering will not work!)

// Servo frequency
const uint8_t SERVO_FREQUENCY = 50; // usually 50Hz, some servos may run smoother @ 100Hz

// WARNING: never connect receiver PWM signals to the "CH" pins in BUS communication mode!

// Servo limits
uint16_t CH1L = 1000, CH1C = 1500, CH1R = 2000; // CH1 steering left, center, right
uint16_t CH2L = 1000, CH2C = 1500, CH2R = 2000; // CH2 transmission gear 1, 2, 3
uint16_t CH3L = 1000, CH3C = 1500, CH3R = 2000; // CH3 Beacons (modes are switched, if position changes from 1000 to 2000us)
uint16_t CH4L = 1350, CH4R = 1650;              // CH4 trailer coupler (5th. wheel) locked, unlocked

// Servo ramp time
uint16_t STEERING_RAMP_TIME = 0; // 0 = fastest speed, enlarge it to around 3000 for "scale" servo movements

#endif

// MN Model 1:12 Land Rover Defender servo configuration profile -------------------------------------------------------------------
#ifdef SERVOS_LANDY

// Servo frequency
const uint8_t SERVO_FREQUENCY = 50; // usually 50Hz, some servos may run smoother @ 100Hz

// WARNING: never connect receiver PWM signals to the "CH" pins in BUS communication mode!

// Servo limits
uint16_t CH1L = 1840, CH1C = 1485, CH1R = 1090; // CH1 steering left 1880, center 1480, right 1080
uint16_t CH2L = 978, CH2C = 1833, CH2R = 1833;  // CH2 transmission gear 1 978, 2 1833, 3 1833
uint16_t CH3L = 1300, CH3C = 1450, CH3R = 1600; // CH3 winch pull, off, release
uint16_t CH4L = 1300, CH4R = 1700;              // CH4 trailer coupler (5th. wheel) locked, unlocked

// Servo ramp time
uint16_t STEERING_RAMP_TIME = 0; // 0 = fastest speed, enlarge it to around 3000 for "scale" servo movements

#endif

// Double Eagle 1:8 Land Rover Defender servo configuration profile -------------------------------------------------------------------
#ifdef SERVOS_LANDY_DOUBLE_EAGLE

#define MODE2_WINCH // Mode 2 is used for winch mode, if defined. The winch is controlled by the CH4 pot and connected to Servo CH3. BUS mode only!
// #define NO_WINCH_DELAY // Use this, if you don't want a winch on / off ramp

// Servo frequency
const uint8_t SERVO_FREQUENCY = 50; // usually 50Hz, some servos may run smoother @ 100Hz

// WARNING: never connect receiver PWM signals to the "CH" pins in BUS communication mode!

// Servo limits
uint16_t CH1L = 900, CH1C = 1600, CH1R = 2200;  // CH1 steering left 900, center 1600, right 2200
uint16_t CH2L = 1900, CH2C = 1000, CH2R = 1000; // CH2 transmission gear 1 1900, 2 1000, 3 1000
uint16_t CH3L = 2000, CH3C = 1500, CH3R = 1000; // CH3 winch pull, off, release
uint16_t CH4L = 1300, CH4R = 1700;              // CH4 trailer coupler (5th. wheel) locked, unlocked

// Servo ramp time
uint16_t STEERING_RAMP_TIME = 0; // 0 = fastest speed, enlarge it to around 3000 for "scale" servo movements

#endif

// WPL C34 Toyota Land Cruiser configuration profile -------------------------------------------------------------------------------------------
#ifdef SERVOS_C34

// Servo frequency
const uint8_t SERVO_FREQUENCY = 50; // usually 50Hz, some servos may run smoother @ 100Hz

// WARNING: never connect receiver PWM signals to the "CH" pins in BUS communication mode!

// Servo limits
uint16_t CH1L = 1940, CH1C = 1600, CH1R = 1140; // CH1 steering left 1990, center 1640, right 1090
uint16_t CH2L = 670, CH2C = 1800, CH2R = 1800;  // CH2 transmission gear 1 978, 2 1800, 3 1800
uint16_t CH3L = 1300, CH3C = 1450, CH3R = 1600; // CH3 winch pull, off, release
uint16_t CH4L = 1300, CH4R = 1700;              // CH4 trailer coupler (5th. wheel) locked, unlocked

// Servo ramp time
uint16_t STEERING_RAMP_TIME = 0; // 0 = fastest speed, enlarge it to around 3000 for "scale" servo movements

#endif

// WPL Ural servo configuration profile -------------------------------------------------------------------------------------------
#ifdef SERVOS_URAL

// Servo frequency
const uint8_t SERVO_FREQUENCY = 50; // usually 50Hz, some servos may run smoother @ 100Hz

// WARNING: never connect receiver PWM signals to the "CH" pins in BUS communication mode!
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

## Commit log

2019-12-07 V0.4: volume offset bug fixed, new sounds
    [Adjustments.h, Rc_Engine_Sound_ESP32.ino, curves.h]
2019-12-08 V0.4: volume offset bug fixed, new sounds, schematic
2019-12-09 V0.5: added PWM horn triggering option, Jaguar car and UP locomotive
2019-12-10 v0.6: fixed slow engine RPM response
    [Adjustments.h, Rc_Engine_Sound_ESP32.ino]
2019-12-10 v0.7: "gap" bug between sounds in PWM mode fixed, 2 sounds in PWM mode
    [Adjustments.h, Rc_Engine_Sound_ESP32.ino]
2019-12-10 v0.8: many new sounds, volume offset bug fixed again
    [Adjustments.h, Rc_Engine_Sound_ESP32.ino]
2019-12-14 v0.9: Humvee Diesel sound and truck pneumatic brake release sound added
2019-12-15 v1.0: engine shut off sequence, truck air brakes
2019-12-16 v1.1: Truck reversing peep sound added
    [Adjustments.h, Rc_Engine_Sound_ESP32.ino]
2019-12-24 v1.51: solved redefinition issue
    [mixerEquation.xlsx]
2019-12-31 v1.7: engine vibration shaker support added
    [Adjustments.h, Rc_Engine_Sound_ESP32.ino]
2020-01-04 v1.8: throttle dependent engine volume, indicator ticking sound, new sounds
2020-01-10 v1.9: initial PPM input support for throttle and steering
2020-01-19 v2.2: vehicle mass simulation (ESC control) added, LED pins changed, Scania R620 sound
2020-01-19 v2.2: vehicle mass simulation (ESC control) added, LED pins changed, Scania R620 sound added
2020-01-20 v2.3: many detail optimisations like brake lights, reversing lights, air brake sound
    [Adjustments.h, Rc_Engine_Sound_ESP32.ino]
2020-01-22 Minor reversing bug fixed, failsafe mode for Serial & PWM communication mode
    [Adjustments.h, Rc_Engine_Sound_ESP32.ino]
2020-02-08 v2.5: 3rd brake light added, realistic top speed, smoother acceleration & deceleration
2020-02-20 v2.7: inertia simulation transmission gear dependent, new horns
2020-02-21 v2.8: virtual clutch added, variable acceleration speed, better brakes
2020-02-22 v2.9: throttle now automatically altered while TAMIYA 3 speed gearbox shifting
2020-02-23 v2.91: minor bugfixes according to readme.md
    [Adjustments.h, Rc_Engine_Sound_ESP32.ino]
2020-02-24 v3.0: clutch engaging changed to prevent it from excessive slipping
    [Adjustments.h, Rc_Engine_Sound_ESP32.ino]
2020-03-08 v3.4: separate Diesel knock with fixed sampling rate, many other changes
    [Adjustments.h, Rc_Engine_Sound_ESP32.ino]
2020-03-14 v3.5: diesel knock triggering bug fixed, new sounds and more
    [Adjustments.h, Rc_Engine_Sound_ESP32.ino]
2020-03-15 Cooling fan sound, Tatra 813 V12, Scania 50 ton added
2020-03-15 v3.6: Cooling fan sound, Tatra 813 V12, Scania 50 ton added
2020-03-20 v3.61: Tatra 813 optimised, new fan & knock sounds
2020-03-25 Initial schematic (without LED & shaker outputs)
    [RC_Engine_Sound_ESP32.brd, RC_Engine_Sound_ESP32.sch]
2020-03-28 v3.7 now supporting 30 pin ESP32 board as well
2020-03-30 Schematic now including PCB layout (for 36 pin ESP32)
    [RC_Engine_Sound_ESP32.brd, RC_Engine_Sound_ESP32.sch]
2020-03-30 v3.8 automatic transmission simulation, PCB files!
2020-03-31 Gerber files included, mounting holes now recognised properly in Gerber export
    [RC_Engine_Sound_ESP32.brd]
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2020-04-05 Final PCB for 30 pin ESP32 available!
    [RC_Engine_Sound_ESP32.brd, RC_Engine_Sound_ESP32.sch]
2020-04-10 Removed faulty Gerber file
2020-04-10 Solved board issues after assembling of first PCB
    [RC_Engine_Sound_ESP32.brd, RC_Engine_Sound_ESP32.sch]
2020-04-11 schematic replaced
2020-04-13 v4.0: failsafe for SBUS implemented
    [Adjustments.h, Rc_Engine_Sound_ESP32.ino]
2020-04-16 PCB v1.1: moved R28 away from trailer connector
    [RC_Engine_Sound_ESP32.brd, RC_Engine_Sound_ESP32.sch]
2020-04-16 30 pin board pic added
2020-05-02 v4.1: automatic 4 speed transmission with torque converter
2020-05-02 v4.11: automatic 4 speed transmission with torque converter
2020-05-09 v4.2: 3, 4 or 6 gears & adaptive shift points for automatic transmission & more
2020-05-24 v4.4: adaptive knock volume, Jeep track hawk , DAF XF added
2020-07-14 v4.5: CATERPILLAR_MODE (dual throttle input) for tanks, diggers etc.
2020-07-18 BOM (Components List) added
2020-07-21 BOM (Components List) updated
2020-07-30 v4.8: throttle fader, documentation, supercharger, improved Jeep trackhawk
2020-08-02 v4.81: Scania naming bug solved
    [Adjustments.h, Rc_Engine_Sound_ESP32.ino]
2020-08-04 v4.82: Missing files for Ural 2 setting added
    [Adjustments.h, Rc_Engine_Sound_ESP32.ino]
2020-08-23 v5.0: switching between idle and rev sound now working seamlessly
2020-08-23 v5.01: CAT 3408 Peterbilt added, configuration error solved
    [Adjustments.h, Rc_Engine_Sound_ESP32.ino]
2020-08-28 v5.1: Jake brake, gearbox neutral, adjustable volume, high / low beam for headlights, new W900A sounds
2020-09-23 v5.3: PWM now faster, Kirovets K700
    PWM performance issues solved, 5 channels instead of 4, improved and new vehicles
    [00_Master.h, 1000HpScaniaV8.h, 1965FordMustangV8.h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]
2020-09-25 v5.4: Volvo FH16, Cummins 12V, R6 knock pattern
2020-10-07 v5.5: channel assignment, virtual 3 speed manual
    [adjustmentsRemote.xlsx]
2020-11-01 v5.7: new SMD PCB, 16 gears, soft switching indicators
    [BOM.xlsx, RC_Engine_Sound_ESP32.brd, RC_Engine_Sound_ESP32.sch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]
2020-11-06 v5.8: MAN TGX 680, SMD board v1.1
    [BOM.xlsx, RC_Engine_Sound_ESP32.brd, RC_Engine_Sound_ESP32.sch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]
2020-11-18 V5.9: new lights options, higher PWM frequency
2020-11-25 Gerbers.zip BOM error fixed
2020-12-07 now including "How To Order Your PCB.pdf"
2020-12-08 v6.2: changes according to README.md
    [SMDbase.stl]
2021-01-20 v6.4: outputs for steering & shifting servo
2021-02-14 v6.5: macOS Big Sur fix
    [Rc_Engine_Sound_ESP32.ino]
2021-02-24 v6.6: new fifth wheel options
    [adjustmentsRemote.xlsx]
2021-03-02 v6.61: 'couplingSampleCount' bug fixed
    [Rc_Engine_Sound_ESP32.ino]
2021-03-06 v6.62: ESC state machine lockup bug fixed
    [2_adjustmentsRemote.h, 3_adjustmentsESC.h, Rc_Engine_Sound_ESP32.ino]
2021-03-07 v6.63: trailer sound fixes
    [2_adjustmentsRemote.h, 6_adjustmentsLights.h, Rc_Engine_Sound_ESP32.ino]
2021-03-13 v6.64: known issues added
    [3_adjustmentsESC.h, Rc_Engine_Sound_ESP32.ino]
2021-03-14 v6.8: STEERING_RAMP_TIME for scale steering movements
2021-03-15 v6.81: bugfixes according to changelog
    [Rc_Engine_Sound_ESP32.ino]
2021-05-08 v6.9: new horn melodies, GMC sierra, Volvo FH, new engine brake option
2021-05-31 v7.1: shifting servo output usable with automatic transmission
2021-06-03 v7.2: Unimog engine brake, bugfixes, indicators as debugger
    [00_Master.h, 2_adjustmentsRemote.h, 3_adjustmentsESC.h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]
2021-06-05 v7.3: many updates according to changelog
    [gearRatios.xlsx]
2021-06-27 v7.5: many improvements according to README.md
    [ESCLinearity.xlsx]
2021-08-22 v7.7: LCD dashboard, Neopixels, SUMD support
    [adjustmentsRemote.xlsx]
2021-09-01 v7.9: excavator bucket rattle, hydraulic load dependent engine RPM drop
    [6_adjustmentsLights.h, Caterpillar323Excavator.h, Rc_Engine_Sound_ESP32.ino]
2021-09-22 v8.0: Many changes and bugfixes according to README.md
    [2_adjustmentsRemote.h, 3_adjustmentsESC.h, 7_adjustmentsServos.h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]
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2021-10-08 v8.11: serious PWM mode bug fixed, other minor changes
    [2_adjustmentsRemote.h, 3_adjustmentsESC.h, 9_adjustmentsDashboard.h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]
2021-10-24 v8.2: Visual Studio Code support. Directory structure changed!
    for details see change log in README.md
    [ESCLinearity.xlsx, RC_Engine_Sound_ESP32.brd, RC_Engine_Sound_ESP32.sch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]
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2021-11-14 v8.4: Magirus Deutz 256 sound, new parameters, sounds reworked
    [00_Master.h, 1965FordMustangV8.h, 2_adjustmentsRemote.h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]
2021-11-17 v8.5: multiple wireless trailer support and much more. See change log
    [adjustmentsRemote.xlsx]
2021-12-18 new SMD board added, trailer SW update v0.3
    [RC_Engine_Sound_ESP32.brd, RC_Engine_Sound_ESP32.sch, SMDbase.stl]
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2022-01-01 v8.8: faster steering servo movement, new 5th wheel option
2022-02-16 v8.9: new wireless trailer lights option
    [BOM.xlsx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]
2022-02-27 v9.0: AIRPLANE_MODE, trailer ramps ESC mode
    [adjustmentsRemote.xlsx]
2022-03-29 Improved serial output and debug info, fixed a few typos
    [6_adjustmentsLights.h, src.ino]
2022-04-19 Servo Debug Typo fixed
    [src.ino]
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2022-05-08 Added Arduino header to every vehicle config file.
2022-05-08 Fixed some sound file (.h) names (mostly upper/lower case typos).
    [00_Master.h]
2022-05-08 v9.2: board definition 1.0.6 now compatible, Neopixel animations
2022-05-12 v 9.3: support for RZ7886 motor driver IC, more ESC parameters
2022-05-18 v 9.4: SBUS baudrate adjustable, ticking noise fixed
    [2_adjustmentsRemote.h, 6_adjustmentsLights.h, src.ino]
2022-05-27 v9.5: battery low discharge protection and more, see change log
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2022-06-30 v9.9.1: SBUS & battery protection bugfixes
    [2_adjustmentsRemote.h, 3_adjustmentsESC.h, 7_adjustmentsServos.h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]
2022-07-11 v9.10.0: STEAM_LOCOMOTIVE_MODE see change log
    [ESCLinearity.xlsx]
2023-02-08 lowered WiFi power, less noise in speaker
    [6_Lights.h, src.ino, webInterface.h]
2023-02-12 v9.12.0 beta 3: adjustable WiFi power and more
2023-05-14 9.13.0-b1 ESC adjustable on 192.168.4.1, Neopixels on CH 4
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2026-03-14 v9.14.0: many changes according to Changelog.md
    - Documentation files in German added
    - Documentation Files made by Frikkie Bester added
    - Mercedes SK 1935 V8 truck added
    - Mercedes SK 1838 V8 truck added
    - Rough terrain crane added
    - CRANE_MODE added (many hydraulic channels)
    - SBUS can now decode 16 instead of 13 channels, used for additional servo outputs in rough terrain crane
    - Hitachi ZW 370-6 wheel loader added
    - FRSKY_TANDEM_HARMONY_LOADER remote profile added for TANDEM XE with touchscreen
    - ESC settings added: HYDROSTATIC_MODE, directionChangeLimit
    - Lights settings added: ROTATINGBEACON_ON_B1, INDICATOR_TOGGLING_MODE
    - Audio2Header.html now including "reversing beep" category
    - RE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
    [Standard Parts List.xlsx, adjustmentsRemote.xlsx, servoCurves.xlsx]

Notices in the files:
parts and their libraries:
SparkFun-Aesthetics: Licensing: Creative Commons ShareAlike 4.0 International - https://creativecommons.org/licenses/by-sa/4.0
